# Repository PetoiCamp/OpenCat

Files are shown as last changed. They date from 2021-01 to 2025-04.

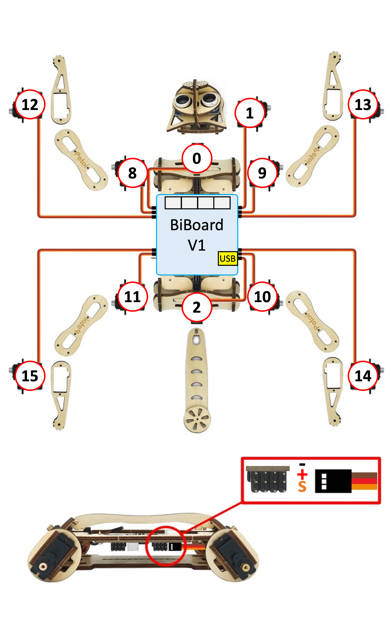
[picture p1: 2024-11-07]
pyUI/resources/NybbleQ1_Wire.jpeg

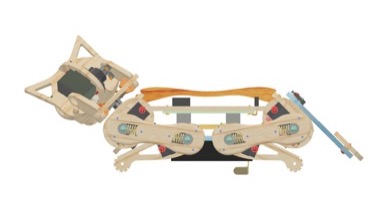
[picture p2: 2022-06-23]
pyUI/resources/Nybble_Rest.jpeg

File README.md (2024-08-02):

# OpenCat

OpenCat is the open-source Arduino and Raspberry Pi-based quadruped robotic pet framework developed by Petoi, the maker of futuristic programmable robotic pets.





Inspired by Boston Dynamics' Big Dog and Spot Mini, Dr. Rongzhong Li started the project in his dorm at Wake Forest University in 2016. After one year of R&D, he founded Petoi LLC and devoted all his resources to developing open source robots. 

The goal is to foster collaboration in quadruped(four-legged) robotic research, education, and engineering development of agile and affordable quadruped robot pets, bring STEM concepts to the mass, and inspire newcomers (including many kids and adults) to join the robotic AI revolution to create more applications.



The project is [a complex quadruped robot system](https://www.petoi.com/pages/petoi-programmable-quadruped-robot-system) for anyone exploring quadruped robotics. We want to share our design and work with the community and bring down the hardware and software costs with mass production. OpenCat has been deployed on all Petoi's bionic palm-sized, realistic lifelike [cute robot cat Nybble](https://www.petoi.com/collections/robots/products/petoi-nybble-robot-cat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) and
[high-performance robot dog Bittle](https://www.petoi.com/collections/robots/products/petoi-bittle-robot-dog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). We now have established a production line and can ship these [affordable robotic kits and accessories](https://www.petoi.com/store?utm_source=github&utm_medium=code&utm_campaign=store) worldwide.

This project provides a base open source platform to create amazing programmable gaits, locomotion, and deployment of inverse kinematics quadruped robots and bring simulations to the real world via block-based coding/C/C++/Python programming languages.  

Our users have deployed many robotics/AI/IoT applications:
- [robot dog with autonomous movement & object detection](https://www.petoi.com/blogs/blog/reid-graves-robotics-ai-applications-with-bittle-robot-dog-raspberry-pi)
- [Raspberry Pi robotics projects](https://www.petoi.com/blogs/blog/raspberry-pi-robotics-projects-with-petoi-open-source-quadruped-robots)
- [NVIDIA Issac simulations and reinforcement learning on our robots](https://www.youtube.com/playlist?list=PLHMFXft_rV6MWNGyofDzRhpatxZuUZMdg)
- [developed visual and lidar-based SLAM with ROS using Bittle and Raspberry Pi](https://www.youtube.com/watch?v=uXpQUIF_Jyk&list=PLHMFXft_rV6MWNGyofDzRhpatxZuUZMdg&index=6)
- [imitation learning using Tiny Machine Learning Models with Petoi Bittle and Raspberry Pi](https://www.learnwitharobot.com/p/imitation-learning-with-petoi-bittle)
- [IoT automation of a robot fleet with AWS to improve worker safety](https://www.petoi.com/blogs/blog/aws-iot-robot-fleet-demo-with-petoi-bittle)
- [3D-Printed Accessories](https://www.petoi.com/blogs/blog/petoi-bittle-bittle-x-robots-3d-printed-robot-accessories)
- build their own [DIY 3D-print robot pets](https://www.petoi.com/pages/3d-printed-robot-dog-robot-cat) powered by OpenCat





We've successfully crowdfunded these two mini robot kits and shipped thousands of units worldwide. 

With our [customized Arduino-Uno board](https://www.petoi.com/products/nyboard-customized-arduino-board) and [high-performance servos](https://www.petoi.com/products/quadruped-robot-dog-bittle-servo-set) coordinating all instinctive and sophisticated movements(walking, running, jumping, backflipping), one can clip on [various sensors](https://www.petoi.com/products/petoi-sensor-pack) and [camera](https://www.petoi.com/products/intelligent-camera-module) to bring in perception and inject artificial intelligence capabilities by mounting a Raspberry Pi or other AI chips(such as Nvidia Jetson Nano) through wired/wireless connections. 
 
Please see [Petoi FAQs](https://www.petoi.com/pages/faq?utm_source=github&utm_medium=code&utm_campaign=faq) for more info.

Also, Check out [all of the OpenCat and Petoi robot user showcases](https://www.petoi.camp/forum/showcase).



## Setup  Process:

OpenCat software works on both Nybble and Bittle, controlled by NyBoard based on ATmega328P. More detailed documentation can be found at the [Petoi Doc Center](https://docs.petoi.com).

To configure the board:

1. Download the repo and unfold. Remove the **-main** (or any branch name) suffix of the folder.

2. Open the file OpenCat.ino, select your robot and board version.
```cpp
#define BITTLE    //Petoi 9 DOF robot dog: 1x on head + 8x on leg
//#define NYBBLE  //Petoi 11 DOF robot cat: 2x on head + 1x on tail + 8x on leg

//#define NyBoard_V0_1
//#define NyBoard_V0_2
#define NyBoard_V1_0
//#define NyBoard_V1_1
```

3. Comment out ```#define MAIN_SKETCH``` so that it will turn the code to the board configuration mode. Upload and follow the serial prompts to proceed.
```cpp
// #define MAIN_SKETCH
```

4. If you activate ```#define AUTO_INIT```, the program will automatically set up without prompts. It will not reset joint offsets but calibrate the IMU. It's just a convenient option for our production line.

5. Plug the USB uploader to the NyBoard and install the driver if no USB port is found under Arduino -> Tools -> Port.

6. Press the upload button (->) at the top-left corner in Arduino IDE.

7. Open the serial monitor of Arduino IDE. You can find the button either under Tools, or at the top-right corner of the IDE.

Set the serial monitor as **no line ending** and **115200** baud rate.
The serial prompts:
```
Reset joint offsets? (Y/n)
Y
```

Input ‘Y’ and hit enter, if you want to reset all the joint offsets to 0.

The program will do the reset, then update the constants and instinctive skills in the static memory.

8. IMU (Inertial Measurement Unit) calibration.

The serial prompts:
```
Calibrate the IMU? (Y/n):
Y
```
Input ‘Y’ and hit enter, if you have never calibrated the IMU or want to redo calibration.

Put the robot flat on the table and don't touch it. The robot will long beep six times to give you enough time. Then it will read hundreds of sensor data and save the offsets. It will beep when the calibration finishes.

When the serial monitor prints "Ready!", you can close the serial monitor to do the next step.

9. Uncomment ```#define MAIN_SKETCH``` to make it active. This time the code becomes the normal program for the major functionalities. Upload the code.
```cpp
#define MAIN_SKETCH
```
When the serial monitor prints "Ready!", the robot is ready to take your next instructions.

10. If you have never calibrated the joints’ offsets or reset the offsets in Step2, you need to calibrate them. If you boot up the robot with one side up, it will enter the calibration state automatically for you to install the legs. Otherwise, it will enter the normal rest state

11. You can use the serial monitor to calibrate it directly. Or you may plug in the Bluetooth dongle, and use the Petoi app (on Android/iOS) for a more user-friendly interface. The mobile app is available on:

* IOS: [App Store](https://apps.apple.com/us/app/petoi/id1581548095)
* Android: [Google Play](https://play.google.com/store/apps/details?id=com.petoi.petoiapp)

You can refer to the calibration section in the user manual (https://bittle.petoi.com/6-calibration) and Guide for the Petoi App(https://docs.petoi.com/app-guide).

12. you can use the infrared remote or other applications (such as the Petoi App, Python, serial monitor ... etc.) to play with the robot (https://bittle.petoi.com/7-play-with-bittle).

For updates:
* star this repository to receive timely notifications on changes.
* visit www.petoi.com and [subscribe to our official newsletters](https://www.petoi.com/pages/subscribe-petoi-newsletter) for project announcements. We also host a forum at [petoi.camp](https://www.petoi.com/forum).
* follow us on [Twitter](https://twitter.com/petoicamp), [Instagram](https://www.instagram.com/petoicamp/), [Facebook](https://www.facebook.com/PetoiCamp/), [Linkedin](https://www.linkedin.com/company/33449768/admin/dashboard/), and [YouTube channel](https://www.youtube.com/c/rongzhongli) for fun videos and community activities.



## Resources:
* [Advanced tutorials made by users](https://www.youtube.com/playlist?list=PLHMFXft_rV6MWNGyofDzRhpatxZuUZMdg)
* [Review, open-box, and demos by users](https://www.youtube.com/playlist?list=PLHMFXft_rV6PSS3Qu5yQ-0iPW-ohu1sM3)
* [OpenCat robot showcase by users](https://www.petoi.com/pages/petoi-open-source-extensions-user-demos-and-hacks)
* [OpenCat robot gallery](https://www.petoi.com/pages/robot-pet-gallery)

OpenCat robots have been used in robotics education for K12 schools and colleges to teach students about STEM, coding, and robotics:
- [robotics education showcases](https://www.petoi.com/blogs/blog/tagged/showcase+education)
- [STEM & Robotics Curriculum & Resources for Teaching Coding & Robotics](https://www.petoi.com/pages/resources-curriculum-stem-coding-robot)
- [Robotics competitions](https://www.petoi.com/blogs/blog/robot-competitions-with-petoi)
- [Petoi robotics contest](https://www.petoi.com/blogs/blog/petoi-spring-2024-robotics-contest-winners)

The [old repository for OpenCat](https://github.com/PetoiCamp/OpenCat-Old) is too redundant with large image logs and is obsolete with no further updates.

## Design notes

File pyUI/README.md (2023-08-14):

# Petoi Desktop App 
## The source codes are written with Tinker in Python3 

The major function modules are the [Firmware Uploader](https://docs.petoi.com/desktop-app/firmware-uploader), [Joint Calibrator](https://docs.petoi.com/desktop-app/calibrator), and [Skill Composer](https://docs.petoi.com/desktop-app/skill-composer). 

**UI.py** is the general entry for all the modules:

- UI.py

-> FirmwareUploader.py

-> Calibrator.py

-> SkillComposer.py

gui

**translate.py** provides multi-language support for the UI. You may help to translate the UI into your language. 

Before running the app, you need to use the included USB adapter or the Bluetooth dongle to connect to a Petoi robot. 

## Pre-compiled binaries

You can download the [pre-compiled binaries](https://github.com/PetoiCamp/OpenCat/releases).

Windows users:
Double-click the exe file to run the app. Keep all the files in the Win folder when moving the app. 

Mac users:
Double-click the dmg file and drag the app to the Application folder. Go to the Application folder and right-click the Petoi icon. Hold the **shift** key, then click **Open**.

## Run the app from the Terminal 
In the case of compatibility issues, or if you want to modify the source and test, you can also run the code from the Terminal. 

The Terminal is a built-in interface on Mac or Linux machines. The equivalent environment on Windows machines is called the Command-Line Tool (CMD). 
It's recommended that you install [Anaconda](https://www.anaconda.com/) to manage your Python environment. It can also provide the Powershell as a Terminal for older Windows machines. 

Depending on your existing Python configuration, you may need to upgrade to Python3 and install the following libraries:

- pyserial
- pillow

You can install them by entering ```pip3 install pyserial pillow``` in the Terminal or use the package manager in Anaconda. 

To run the code:
1. In the Terminal, use the ```cd``` command to navigate to the ```OpenCat/pyUI/``` folder. You can use the Tab key to auto-complete the path name. 
2. After entering the pyUI/ folder, enter ```ls``` and ensure you can see the UI.py and other python source codes listed. 
3. Enter ```python3 UI.py```.

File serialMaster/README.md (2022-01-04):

## serialMaster User Guide

**Preparation**

1.  Install python (version≥ 3.6, such as Anaconda3-5.2.0-Windows-x86_64.exe)
    
2.  Install pyserial library (version 3.5)
    
**Run script**

The script program will automatically identify the serial port number at the very beginning of the run, and complete the connection.

Generally, when using a USB adapter to connect to Nybble (or Bittle), there is only one serial port number:

USB serial port number

When using the Bluetooth module, there are two serial port numbers:

Bluetooth serial port number

Open Terminal (such as Anaconda Prompt), enter the path where the script is located (***\serialMaster), you can use the following command to run the script:

**Method 1**: Run the **ardSerial.py**

***\serialMaster>python3 ardSerial.py kbalance

Parameters: **kbalance** is a serial port command representing Nybble (or Bittle) skills.

Of course, you can also run this script without any parameters:

***\serialMaster>python3 ardSerial.py

When the system recognizes that there are multiple serial port numbers, the script will print out the following prompt message at the very beginning of the run:

**If there is no response after you input the serial command in the terminal, you should close the terminal first, then change the value of "bluetoothPortIndex" in the ardSerial.py (line:128)to connect to another blue tooth serial port, then reopen the terminal and rerun the script.**

When the script formally starts running, the following prompt information is printed out:
**You can type 'quit' or 'q' to exit.**

Next, you can enter serial port commands in Terminal to control Nybble (or Bittle) to do various interesting actions e.g.

kbalance           # Command to control Nybble(or Bittle) to stand normally

m 0 -30 0 30       # Command to control Nybble(or Bittle) head to swing left and right

**Method 2**: Run a custom script, e.g.  **example.py**

***\serialMaster>python3 example.py

The list **testSchedule** in example.py is used to test various serial port commands. Run the following script code to see the execution effect of each serial port command in the list:

for task in testSchedule:
	wrapper(task)

You can also refer to the content of the **stepUpSchedule** list (in***\serialMaster\demos\stepup.py), write a list of behaviors according to your actual needs, and realize your creativity.

**Note**: When running the scripts under the path **"***\serialMaster\demos"**, you must first use the **"cd demos"** command to enter the path where the scripts are located (\serialMaster\demos), and then use the **python3** command to run the script. e.g. 
***\serialMaster\demos>python3 stepup.py

Explanation of the serial port commands in the list**testSchedule**:

**['kbalance', 2]**
-   'kbalance' indicates the command to control Bittle to stand normally
-   2 indicates the postponed time after finishing the command, in seconds

**['m', [0, -20], 1.5]**
- m indicates the command to control the rotation of the joint servo
-   0 indicates the index number of joint servo
-   -20 indicates the rotation angle (this angle refers to the origin, rather than additive) the unit is degree
-   1.5 indicates the postponed time after finishing the command, in seconds. It can be a float number

**['m', ['m', '0', '45', '0', '-45', '0', '45', '0', '-45'], 2]**

Using this format, multiple joint servo rotation commands can be issued at one time, and these joint servo rotation commands are executed **SEQUENTIALLY**, not at the same time.
The meaning of this example is: the joint servo with index number 0 is first rotated to the 45 degree position, and then rotated to the -45 degree position, and so on. After these motion commands are completed, the next command will be executed after a 2-second delay.

**['M', ['M', '8', '-15', '9', '-20'], 2]**

Using this format, multiple joint servo rotation commands can be issued at one time, and these joint servo rotation commands are executed **AT THE SAME TIME.**
The meaning of this example is the joint servos with index numbers 8, 9 are rotated to the -15, -20 degree positions at the same time. After these motion commands are completed, the next command will be executed after a 2-second delay.

**['d', 2]**
-   d indicates the command to put the robot down and shut down the servos
-   2 indicates the postponed time after finishing the command, in seconds

**['c', 2]**
-   c indicates the command to enter calibration mode
-   2 indicates the postponed time after finishing the command, in seconds. After these motion commands are completed, the next command will be executed after a 2-second delay.

**['c', [0, -9], 2]**
-   c indicates the command to enter calibration mode
-   0 indicates the index number of joint servo
-   -9 indicates the rotation angle, the unit is degree
-   2 indicates the postponed time after finishing the command, in seconds

Using this format, you can enter the calibration mode to calibrate the angle of a certain joint servo.
**Note**: If you want the correction value in this command to take effect, you need to enter the "**s"**command after executing this command.
The meaning of this example: the joint servo with serial number 0 rotates -9 degrees. After these motion commands are completed, the next command will be executed after a 2-second delay.

**['i', [8, 50, 9, 50, 10, 50, 11, 50, 0, 0], 3]**
-   i indicates the command to rotate multiple joint servos at the same time
-   8, 9, 10, 11, 0 indicate the index numbers of joint servos
-   50, 50, 50, 50, 0 indicate the rotation angle (this angle refers to the origin, rather than additive ), the unit is degree
-   3 indicates the postponed time after finishing the command, in seconds
 
**['l', [20, 0, 0, 0, 0, 0, 0, 0, 45, 45, 45, 45, 36, 36, 36, 36], 5]**
-   l indicates the command to control all joint servos to rotate at the same time (currently the command supports 16 degrees of freedom, that is, 16 servos)
-   20,0,0,0,0,0,0,0,45,45,45,45,36,36,36,36 indicate the rotation angle of each joint servo corresponding to 0-15 (this angle refers to the origin, rather than additive), the unit is degree
-   5 indicates the postponed time after finishing the command, in seconds

**['b', [10, 255], 2]**
-   b indicates the command to control the buzzer to beep
-   10 indicates the music tone
-   255 indicates the lengths of duration, the value range is 0~255 
-   2 indicates the postponed time after completing the pronunciation, in seconds

**['b', ['b', '14', '90', '14', '90', '21', '90', '21', '90', ‘23', '90', '23', '90', '21', '180'], 5]**
-   b indicates the command to control the buzzer to beep
-   '14', '14', '21', '21', ‘23', '23', '21' indicate the music tones
-   '90', '90', '90', '90', '90', '90', '180' indicates the lengths of duration
-   5 indicates the postponed time after the music melody is played, in seconds

Using this format, multiple tone pronunciation commands can be issued at one time, and a simple melody can be played.
The meaning of this example is: play a simple melody, and delay 5 seconds after the music melody is played.

For the description of other serial port commands, please refer to Chapter 7 of the Petoi Bittle User Manuals:
[7 🕹 Play with Bittle](https://bittle.petoi.com/7-play-with-bittle)

Please help Nybble and Bittle find their sparks. Wish you have fun!

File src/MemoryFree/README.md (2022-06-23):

This is the excellent MemoryFree library from http://www.arduino.cc/playground/Code/AvailableMemory.

I am hosting it here so there is a quick and easy way to pull it down.

(20 Mar 2015) Repository updated with code from http://playground.arduino.cc/code/AvailableMemory

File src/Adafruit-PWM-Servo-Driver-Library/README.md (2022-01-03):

# Adafruit PCA9685 PWM Servo Driver Library 

This is a library for our Adafruit 16-channel PWM & Servo driver, shield or FeatherWing



Pick one up today in the adafruit shop!
  * https://www.adafruit.com/products/815
  * https://www.adafruit.com/product/1411
  * https://www.adafruit.com/product/2928

These drivers use I2C to communicate, 2 pins are required to interface.

Adafruit invests time and resources providing this open source code, please support Adafruit and open-source hardware by purchasing products from Adafruit!

Written by Limor Fried/Ladyada  for Adafruit Industries. BSD license, check license.txt for more information. 

All text above must be included in any redistribution

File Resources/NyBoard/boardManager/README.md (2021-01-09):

# Arduino IDE Board Manager

Adds the NyBoard board definition through the *Arduino 1.6.4 (and later)* board manager rather then editing `boards.txt` directly as described at https://github.com/PetoiCamp/OpenCat/wiki/Software-setup.

## Usage

1. Open the Arduino IDE application

2. Open the `Preferences...` panel

3. In the `Additional Boards Manager URLs` field, add `https://raw.githubusercontent.com/PetoiCamp/OpenCat/master/Resources/NyBoard/boardManager/package_petoi_nyboard_index.json`. If there are already URLs listed in this field, separate them with commas or click on the icon next to the field to open up an editor and add this URL to a new line.

4. Click on the `OK` button to close the `Preferences...` panel (you may need to do this for the `Additional Boards Manager URLs` editor first, if you opened it up in the previous step)

5. Open the `Boards Manager...` window with the `Tools` -> `Board: XXXX` -> `Boards Manager...` menu item.

6. In the `Filter your search...` field, type `NyBoard`

7. Select the entry and click on `Install`

8. Click on the `Close` button

9. Select `ATmega328P (5V, 20 MHz) NyBoard` from the `Tools` -> `Board: XXXX` menu and enjoy!

## Updating the Board Definition

This section should not be necessary for most users and is included only for reference. As this is my first foray into using the Boards Manager, these steps may change slightly as necessary and I will try to keep this updated for reference.

1. Any additions to the `NyBoard-0.1` directory or changes to `NyBoard-0.1/boards.txt` require the following additional steps (update version numbers as appropriate):

  A. The archive file `NyBoard-0.1.x.tar.bz2` needs to be rebuilt

    i. Mac or Linux, use: `tar -cjf NyBoard-0.1.x.tar.bz2 NyBoard-0.1`

    ii. *TBD* need Windows equivalent

  B. Update `pacakge_petoi_nyboard_index.json` as follows:

    i. Update the `"version"` field to match the new version number (e.g. "0.1.x")

    ii. Update the `"url"` and `"archiveFileName"` fields to match the new archive name.

    iii. Update the `"size"` field to match the new archive file size

    iv. Update the `"checksum"` field to match the new archive file

      a. Mac or Linux use: `openssl dgst -sha256 NyBoard-0.1.x.tar.bz2` to get this value

      b. *TBD* need Windows equivalent

  C. Alternatively, if you wish to keep multiple versions of the board definition around, you can copy the entire entry in `"platforms"` (lines 12 - 31), add a comma after the closing brace of the last entry in `"platforms"`, paste the copy to the next line (before the closing bracket) and make the changes in **B** to the new entry.

2. Changes to the other informational fields of `pacakge_petoi_nyboard_index.json` should not require rebuilding the archive or modifying the file size or checksum values.

## Reference

* https://github.com/PetoiCamp/OpenCat/wiki/Software-setup
* https://github.com/arduino/Arduino/wiki/Arduino-IDE-1.6.x-package_index.json-format-specification

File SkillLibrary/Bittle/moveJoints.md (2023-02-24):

# moveJoints
Note: A test case to send the movement to the smartphone app.

Model: Bittle

Creator: Rz Li

Country: China

Date: Feb 10, 2023

# Token
I

# Data
{
8, -15, 9, -20};

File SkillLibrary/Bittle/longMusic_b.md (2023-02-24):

# longMusic_b
Note: A test case to send the long music to the smartphone app.

Model: Bittle

Creator: Rz Li

Country: China

Date: Feb 10, 2023

# Token
b

# Data
{ 
14, 8, 14, 8, 21, 8, 21, 8, 23, 8, 23, 8, 21, 4, 19, 8, 19, 8, 18, 8, 18, 8, 16, 8, 16, 8, 14, 4, 21, 8, 21, 8, 19, 8, 19, 8, 18, 8, 18, 8, 16, 4, 21, 8, 21, 8, 19, 8, 19, 8, 18, 8, 18, 8, 16, 4,  14, 8, 14, 8, 21, 8, 21, 8, 23, 8, 23, 8, 21, 4, 19, 8, 19, 8, 18, 8, 18, 8, 16, 8, 16, 8, 14, 4};

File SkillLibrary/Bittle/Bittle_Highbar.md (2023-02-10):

# Highbar
Note: Make Bittle roll on a high bar 111 times. Change the 111 to -1 to make it infinite. You need to install the [hooks](https://github.com/PetoiCamp/NonCodeFiles/tree/master/stl/BittleHighbarHooks) on Bittle's front hands. 

Model: Bittle

Creator: David Lin

Country: China

Date: July 18, 2022

# [Demo](https://youtu.be/kam61UxwSVc)

# Token
K

# Data

{
  -3,   0,   0,   2,
   1,   2, 111,
   0,   0,   0,   0,   0,   0,   0,   0, -61, -61,  30,  30,  45,  45,  75,  75,  32,   0,   0, -90,
   0,   0,   0,   0,   0,   0,   0,   0,  28,  28,  21,  21,  25,  25,  44,  44,  48,   0,   0,  10,
   0,   0,   0,   0,   0,   0,   0,   0, -61, -61,  30,  30,  45,  45,  75,  75,   0,   0,  -1, -90,
};

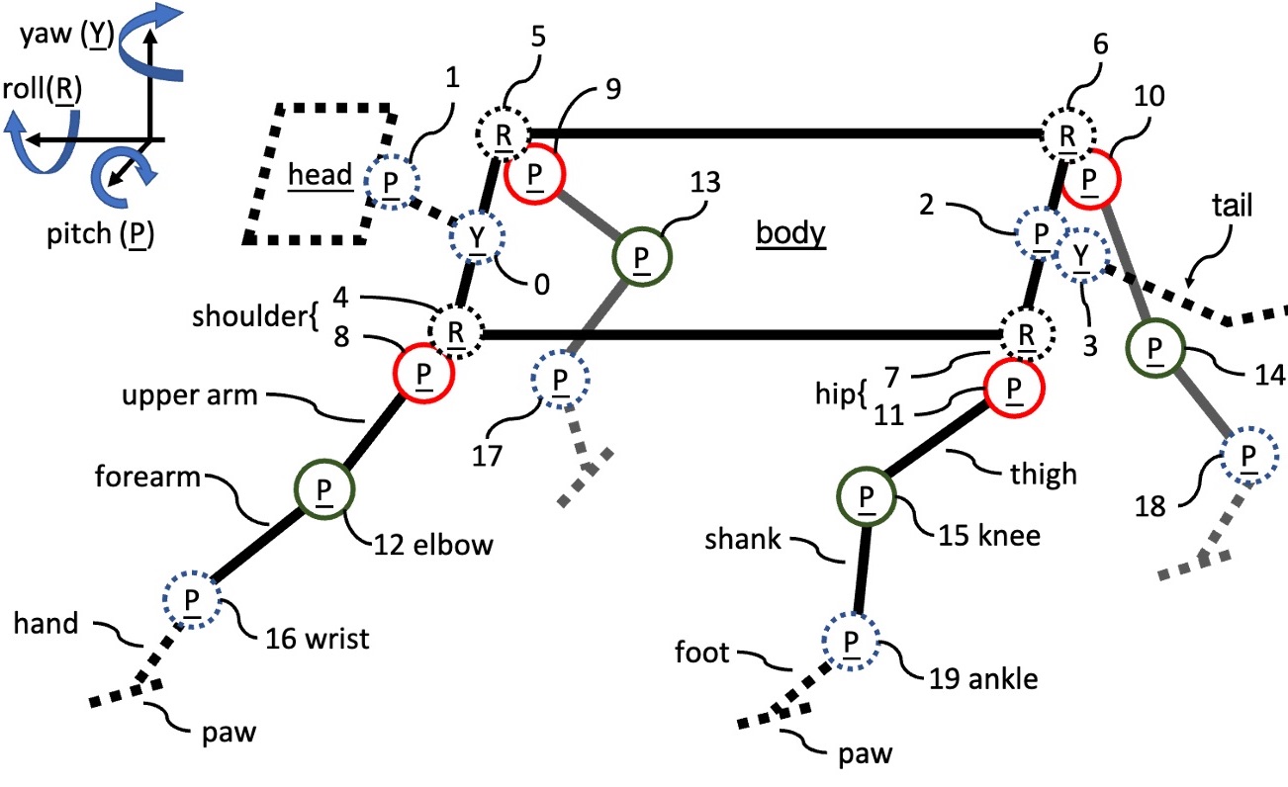
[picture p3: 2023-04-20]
pyUI/resources/DoF16_Stand.jpeg

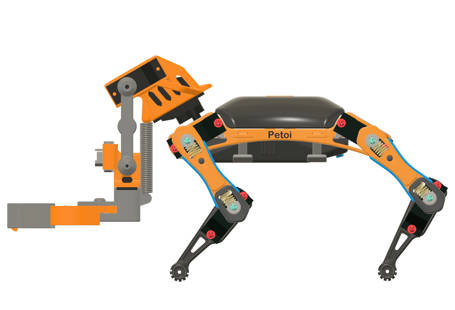
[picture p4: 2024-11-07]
pyUI/resources/BittleX+Arm_Stand.jpeg

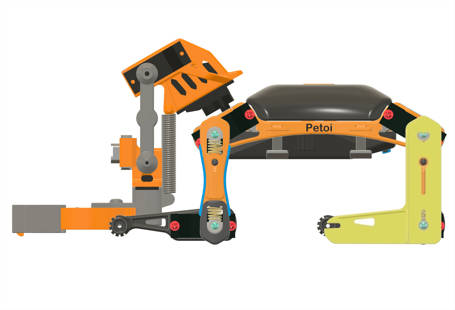
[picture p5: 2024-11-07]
pyUI/resources/BittleX+Arm_Ruler.jpeg

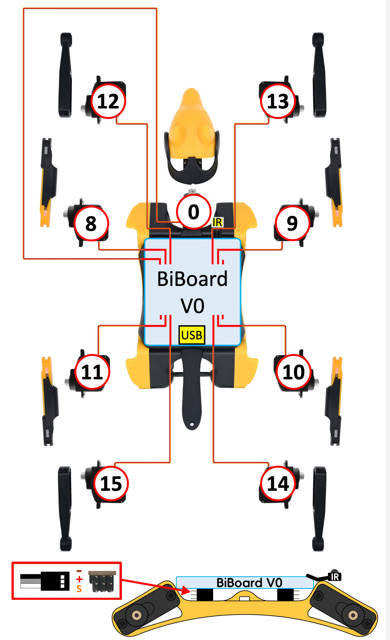
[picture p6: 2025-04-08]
pyUI/resources/BittleX0_Wire.jpeg

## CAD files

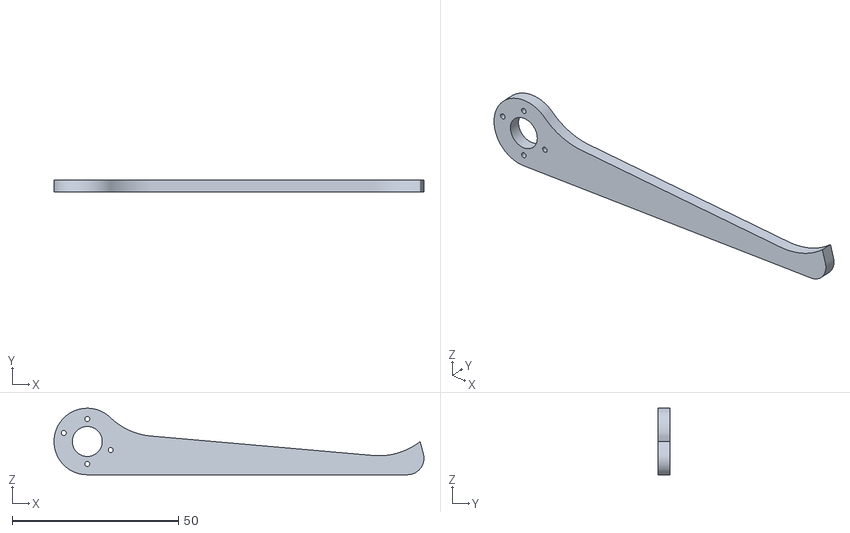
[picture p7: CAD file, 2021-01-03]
ModuleTests/testServo/servoTorqueArm.stl
111.2 x 3.50 x 20.0

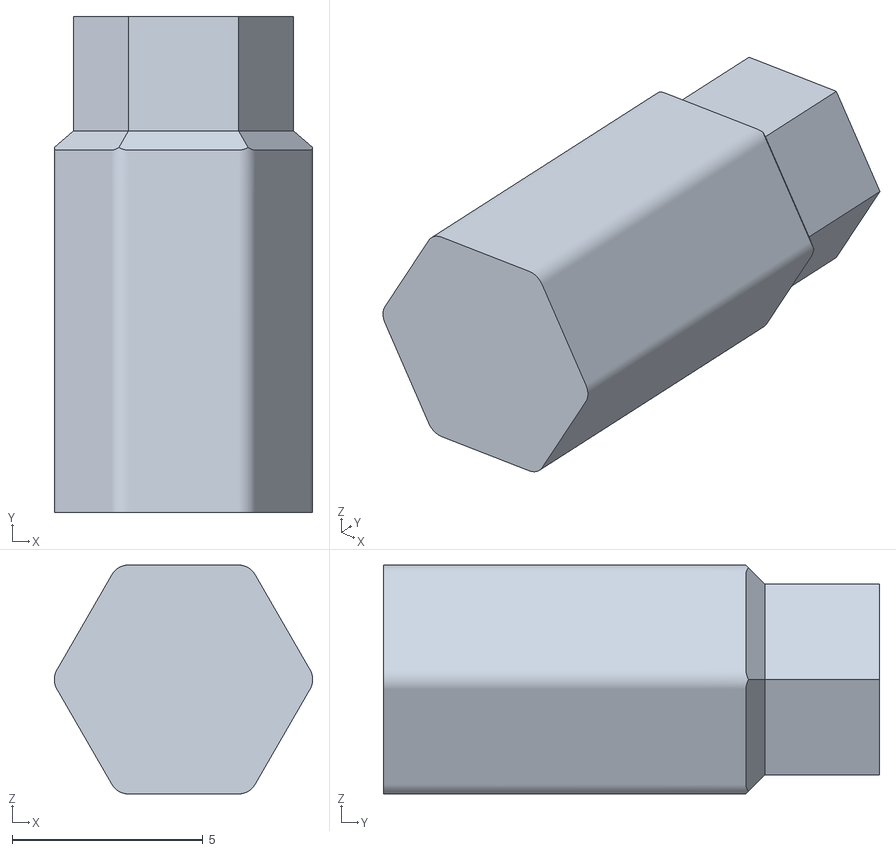
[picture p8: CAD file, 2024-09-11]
pyUI/resources/tool.stl
6.77 x 13.0 x 6.00

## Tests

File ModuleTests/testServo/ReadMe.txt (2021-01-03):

The video for the tests can be found at https://youtu.be/vCvjGVeO57g

Datasheet is at https://docs.google.com/spreadsheets/d/1R2a6Q3H9Heo5MBXjv3MdyxipxWbeRYw3lmymrDakhaY/edit?usp=sharing

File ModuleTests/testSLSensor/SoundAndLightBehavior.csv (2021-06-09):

LIGHT | READING | THRESHOLD
brighter | lower
darker | higher | 850
LIGHT |  | SOUND
_LEVEL | _CHANGE | _LEVEL | _BEHAVIOR
dark |  | low | rest
 |  | high | sit
high |  | low | sit
 |  | high | stand
 | fast light
 | fast dim
bright |  |  | proportional

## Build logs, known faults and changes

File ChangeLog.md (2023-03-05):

# Change Log

## Mar6, 2023
* Recover the skillName stored in **newCmd** array because the newCmd's memory is altered when formatting new skill data. 
* Fix the segfault caused by different string terminators: '\0', '\n', or '\~'.
* Fix the casting between int, char, and int8_t in the template function arrayNCPY().
* When turning a joint instruction into a new posture, allow large joint angles to be stored into an int8_t array. 
* Fix the positive feedback when gyro data is combined into targetAngles.
* SkillComposer: Disable the Gyro and Random buttons.
* ardSerial: Simplify the slicing algorithm when sending long commands.
* Differentiate the serial timeout for long commands over Bluetooth.
* Simplify some skills to save memory. 
* Safer auto-connection algorithm when trying to connect to a camera that's not connected to any alternative addresses. 
* Mobile app: Find the optimal delay between the mobile app's package slices to avoid overflow or timeout on the mainboard. 
* Add a token 'S' to toggle on/off the boot-up melody. 
* Add a macro to inverse the servo's rotation directions.
* Allow the robot to detect the falling-over event and recover even in turbo mode. 
* Desktop App: Add traditional Chinese and German translations. 

## Mar 1, 2023
* Combine the **newCmd** array used for receiving different kinds(ASCII/Binary, long/short) of serial commands. 
* Simplify the token cases into upper/lower letters for Binary/ASCII encodings.
* Shift the skill angle data to the end of the **newCmd** array. It allows new incoming messages to be stored at the beginning of the **newCmd** array while keeping the skill angles unchanged so that the previous skill can resume after finishing the current non-skill command. 
* It now supports much longer commands and skills, such as a behavior with **23** frames (23 * 20 + 7 = 467 bytes), a gait with (467-4)/8 = **57** frames or a long melody with 467/2 = **233** notes. On BiBoard, it supports a behavior with **125** frames (125 * 20 + 7 = 2507 bytes), a gait with (2507-4)/8 = **312** frames or a long melody with 2507/2 = **1253** notes.
* Overflow protection when the incoming message is longer than the size of **newCmd** to avoid a crash. 
* Redesign the voice commands table and their encodings. 
* Add an alias skill "up" for "balance" to save memory and convenience. 
* Move the keys of the customized voice commands to PROGMEM.
* Add new skills:

| New Skill Name | Serial Code |
|---|:---|
|hug 	|khg |
|handstand  |khdsd  |
|hands up |khu 	  |
|handshake	|khsk  	|
|sniff		  |ksnf	  |
|dig	 	|kdg	  |
|scratch |kscrh  |
|be table 	|ktbl	  |
|boxing	  	|kbx	  |
|kick		 |kkc	  |
|come here	|kcmh	  |
|high five	|kfiv	  |
|jump		 |kjmp	  |

* With so many new skills saved to the I2C EEPROM, fix the overflow (wrapped overwriting) when a long 'K' skill data is written to the nearly full memory.
* 'T' token is used to extract the last transferred skill data. Fixed the segfault when a newly configured board has never received a 'K' command but is required to read from an unknown memory. 

## Feb 25, 2023
* Unbind the free joints' motion during walking and keep balancing reaction after the i,I,m,M commands. The free joints are unrelated to walking and balancing. By default, they move by trigonometric functions synced with the legs' pace. If a command requires specific joint movement, it will be unbound and taken over by the higher-level controller. Using the token 'i' or 'I' without more argument will re-bind them to the legs' motion.

When sending joint instructions, the rules are:

| |All are free joints (head, tail, etc.) |Contain joints related to walking|
|:---:|---|---|
|Gait			 |move in perform() => gait  	  |move in tranform() => convert to a new posture	|
|Posture |move in perform() => posture  |move in tranform() => convert to a new posture	|
|Non-skill |move in transform() => lastToken|move in tranform() => convert to a new posture => lastToken|

* Allow explicitly assigning directions of skills. Only the neutral and the leftward skills are stored in the skill table with the suffix -F (only for gaits), -L, or no capitalized letter in the key. Previously all skills are called with random directions, except the gaits. 

Let Name be the skill's name. The new rules are:

| | Match? |Mirror it? |
|---|:---:|:---:|
|gaitF  |All characters |N |
|nameL  |All characters |N |
|nameR  |the first n-1 chars  |Mirror nameL |
|name		|All characters |Random	 |
|nameX  |All characters 	 |Random |

* Debug the creation, pop, and deletion of TaskQueue for safer and more efficient memory management. Optimize the corresponding examples for light, touch, pir, gesture, camera, and voice sensors.

## Feb 10, 2023
* Allow controlling head group while walking.
* Solve serial overflow.
* Add random skill command: kx. It can call a random skill in the preset skill list. 
* Add macros to disable some unused tokens to save space.

## Feb 7, 2023
* Improve the serial read logics. 
* Print software version on boot up.
* Add demos for pir, touch, light modules.
* Allow sending long (450 bytes or 225 notes) melody over the serial port.

## Feb 1, 2023
* Add task queue within the Arduino code. A sequence of tasks can be performed without the need of another master computer. 
* Add demo code for 10 customized voice commands. 

## Jan 19, 2023
* Allow manually select the serial port when the automatic algorithm fails.

## Jan 12, 2023
* Add demo code for the voice command module. 
* SkillComposer: Allow importing multiple skills from InstinctX.h.

## Jan 5, 2023
* Avoid the servos' shaking when booting up.
* Add demo code for the gesture module.

## Dec 29, 2022
* SkillComposer: Avoid freezing when dragging the joint sliders.

## Dec 26, 2022
* Allow a unplug and replug algorithm to tell the intended serial port.
* SkillCompser: Read the robot's name when starting up.

## Dec 13, 2022
* Improve the self-calibration algorithm of PCA9685

## Dec 7, 2022
* SkillComposer: Show warning forlower Python versions.

## Nov 28, 2022
* FirmwareUploader: Support BiBoard.

## Nov 10, 2022
* Create test8266Master.ino that can control the robot's motion in sequence.

## Oct 26, 2022
* Move the detailed initializing functions in **OpenCat.ino**'s setup() to OpenCat.h. 
* Add a simple example to elaborate the integration of customized sensors. You need to enable "#define OTHER_MODULES" to see its effects. 

## Aug 31, 2022
* Add a watchdog to reset the board if the initialization for MPU or skills fails.
* At the last stage of the first configuration process (with #define MAIN_SKETCH commented out), provide an optional step to calibrate the PCA9685's PWM frequency. The calibration value is saved in the EEPROM table to be loaded by the main sketch. 
* Change the unit of the duration for music notes ('b' and 'B' token) from duration (miliseconds) to half notes (use 2, 4, 8 to represent 1/2, 1/4, 1/8).
* For Bittle: Add front flip, roll left, roll right, and tune back flip. It's better to remove its head to perform those tricks. 
* Shrink the size of codes for getting and saving MPU offsets.
* Won't repeat the last behavior after roll recover.
* ESP8266WiFiController: won't refresh the page after sending command to save time
* ESP8266WiFiController: Simplify the cases on the main command page with a dictionary. 
* Add some new moduleTest codes

## May 8, 2022
* pyUI/ui.py: Add names to trigger axis
* pyUI/ui.py: Optimize the layout for Windows machines
* pyUI/ui.py: Add add hover tips to some buttons

## May 4, 2022
* pyUI/ui.py: Import and export files

## May 2, 2022
* pyUI/ui.py: Improve performance with large angles
* pyUI/ui.py: Show connected ports
* pyUI/ui.py: Improve logic and workflow for connecting multiple robots
* pyUI/ui.py: Support connect to one or all robots dynamically
* pyUI/ui.py: Improve global orientation and translation sliders
* pyUI/ui.py: Change dial buttons from regular buttons to press-down buttons

## Apr 30, 2022
* pyUI/ui.py: Mirror single frame during editing
* pyUI/ui.py: Fix bug in the loop structure when exporting 

## Apr 29, 2022
* pyUI/ui.py: Add binders (both positive and negative) for joint sliders to control several joints together.
* pyUI/ui.py: Can control multiple robots at once. 
* ardSerial: Get return value from threads.

## Apr 24, 2022
* pyUI/ui.py: Support loading and sending large angles
* pyUI/ui.py: Optimize panel sizes

## Apr 22, 2022
* pyUI/ui.py: Support selecting different robot models. Update the center image for the model. 
* pyUI/ui.py: Support different lanuguages.
* pyUI/ui.py: Support importing and exporting a multi-frame skill as a behavior or gait. A single frame will always be exported as a posture.
* pyUI/ui.py: Update the skill frame's state for delete operations.
* pyUI/ui.py: Check the format of skill data that's manually entered. Pop up a warning window.  

## Apr 20, 2022
* pyUI/ui.py: Support trigger axis and angles for behaviors
* pyUI/ui.py: Allow stop when playing frames
* Add a button to connect and disconnect the robot in the "State Dials" block
* Change the texts of the state dials to indicate their states

## Apr 19, 2022
* pyUI/ui.py: Support importing existing skill array and editing them frame by frame. Speed and delay are included. The trigger axis of behaviors has not been implemented.
* pyUI/ui.py: Export the skill to the robot and print the skill data array in the terminal. 

## Apr 6, 2022
* Add ui.py in pyUI to allow changing the robot's postures and body tilts with sliders. 
* Improve the structure of ardSerial.py to allow continuous inputs when it's used as a commandline tool. 
* Fix a bug when a static posture is called after a gait by resetting the frame to 0.

## Mar 29, 2022
* Use dataBuffer to hold the incoming serial commands to allow a longer melody and other instructions. newCmd will only be used to hold skill names that are shorter. 
* Save the serial skill data from the dataBuffer to I2C EEPROM so that it can be recalled. 

## Mar 20, 2022
* A schedulerToSkill function in serialMaster to summerize the motion commands and generate a new skill array that can be directly used in the instinct.h.
* Design a convenient macro switch for regular walker, ultrasonic, and voice modes. 
```cpp
//you can activate the following modes (they will diable the gyro to save programming space)
//allowed combinations: RANDOM_MIND, ULTRASONIC, RANDOM_MIND + ULTRASONIC, VOICE
//#define RANDOM_MIND     //let the robot do random stuffs. use token 'z' to activate/deactivate
//#define ULTRASONIC      //for Nybble's ultrasonic sensor
//#define VOICE           //for LD3320 module
```

## Mar 17, 2022
### OpenCat2.0 is pushed to the branch 2.0 for beta testers.
### New Features:
* **Complete redesign of the code structure to make it easier to understand and insert 3rd party codes.**
* **Combine WriteInstinct.ino and OpenCat.ino into a single OpenCat.ino.** Use the ```#define MAIN_SKETCH``` macro to switch between the modes. 
* Fixed many bugs in the original workflow. For example, the robot no longer skips commands randomly.
* Improved the smoothness of motion and the speed of balance adaption. 
* A better documented serialMaster Python module and provide a command scheduler in example.py. 
* **Designd a new token "K"** to send a whole skill array from the Python serial master through serial in realtime then run it locally on the robot.
* Optimized the token definitions. Print the token after finishing one task as a confirmation to the master program. 
* Used a new MPU6050 function to avoid using the interrupt pin. **Accelerate the IMU calibration process.** 
* Enter the joint calibration state by booting up the robot with one side up. 
* Write a formalized servo class inherited from the AdafruitPWM servo library. Make it easier to change parameters of 3rd party servos.
* **Use the built-in tone function to generate clean beeps and melody.**
* Add random actions for the robot to make it more life-like. Use token ‘z’ to turn on/off the feature. 
* Add angle limits to avoid most cases of of self-collision.
* Put the skill-related functions into the Skill Class. Combine reused code blocks into single functions.
* Make more use of the EEPROM and PRGMEM memory to save resources for flash and SRAM.
* Mirror rightward gaits from the leftward gaits, to save static memory. 
* Allow both “newline” and “no line ending” for the serial monitor.
* Add support for LD3320 voice recognition module (the current code works for Chinese).

## Jan 30, 2022
* Fix type conversion warnings of skill data.
* Add demo for testBuzzer.ino using Arduino's built-in tone function. However, it cannot be used for the main program because ATmega328P has only two timers, used up by the IR and IMU. 

## Jan 11, 2022
* Create a mirror function to allow the robot pick random directions of behaviors. It makes the robot more unpredictable and helps it get rid of an infinite loop, such as failed fall-recovering against a wall.  

## Jan 3, 2022
* Put the dependent libraries within the OpenCat folder so that no more downloading is required to configure OpenCat's environment in Arduino. 

It's nasty to include the **src/** libraries here rather than Arduino's desinated library folder, especially when we have to duplicate the **src/** in two layers within the same project folder.  

We do this only to help those users who are new to Arduino and complained about the difficulties of configuring the Arduino environment. You may find more informative comments within those library files. 

## Dec 29, 2021
* Organinzed serialMaster/ and its demo codes
* fixed the divide by zero bug in calibratedPWM()

## Dec 11, 2021
* Fix bug of "wrong key!" messages after g, p

## Dec 3, 2021
* Modified the "hi" behavior of Nybble so its tail will not push Nybble over;
* Replaced the "look up" behavior with "stand". Make sure you hold Nybble when first trying it. 

## Nov 28, 2021
* Add the march gait that only works well with gyro off; 
* Fix many typos with the help of Grammarly.

## Sep 29, 2021
* Print the robot's state (paused and gyro) when "g" and "p" is entered:

| State  | True  | False |
|:---|:---|:---|
| Pause | P (paused) | p (unpaused) |
| Gyro | G (on) | g (off) |

## Sep 26, 2021
* Move the codes for EEPROM to function configureEEPROM() in OpenCat.h;

## Sep 18, 2021
* Copied the required files of IRremote library to OpenCat/src/ to help new Arduino users config the environment. 
* Cancel "pause" of motion if other commands are received. 

## Sep 16, 2021
* Move the EEPROM related functions from WriteInstinct.ino to OpenCat.h.
* Added a "stand" behavior for Nybble so that it can stand up with its hind legs and tail. 

## Sep 9, 2021
* Print the list of calibration offsets before the joints' movements to help the App read the values.

## Aug 31, 2021
* Moved the device's model info (Nybble/Bittle) to the top of booting printouts.
* Added a shorter encoding for the IR remote to save flash by about 178 Bytes.

## Aug 25, 2021
* Added an 'M' token to move multiple indexed joints to angles (ASCII format entered in the serial monitor) simultaneously;
* Re-arranged the IR keymap for the new customized IR panel.

## Jun 29, 2021
* OpenCat.ino will print out the model name (Bittle/Nybble) at booting up.
* Moved #define I2C_EEPROM to the beginning OpenCat.h.

## Jun 7, 2021

* Adjusted the threshold voltage so that Bittle will keep beeping when the battery goes under 6.5V, a few moments before the battery power shuts off;
* Adjusted the gaits so that the elbow won't hit the body in the accelerated phase. 
* The trot on key "1" is tuned to be faster.
* Removed the running gait on the IR remote key "2" and replaced it with "check around" behavior previously on key "3";
* Assigned a "play dead" trick to IR remote key "3". Bittle will fall on its back then roll back (if the gyro is activated);
* Removed the behavior when the robot is tilted at a large angle to avoid an occasional bug. Will put the behavior back if the bug can be fixed; 
* Added an auto-detection code for a new sound&light sensor connected to the analog Grove pin. Some new automated behaviors are being developed. The code block won't be active if the sensor is not connected to the Analog Grove socket;

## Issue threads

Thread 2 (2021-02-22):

OpenCat.ino Sketch to big to compile

loeweh, 2021-02-22:
Hi,

downloaded OpenCat.ino. It does not compile. Error is:

Sketch uses 33764 bytes (104%) of program storage space. Maximum is 32256 bytes.
Global variables use 1344 bytes (65%) of dynamic memory, leaving 704 bytes for local variables. Maximum is 2048 bytes.
Sketch too big; see http://www.arduino.cc/en/Guide/Troubleshooting#size for tips on reducing it.

Updated libraries to the latest.

Any idea?

BR Heiko

borntoleave, 2021-02-22:
You need to download version 2.6.1 of the IRremote library and set the
unused encoders to 0s.
More detailed instructions are mentioned in chapter 4 of the user manual at
bittle.petoi.com.

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

--
~~
Rongzhong Li, PhD
http://borntoleave.github.io

regularfry, 2021-02-24:
Can we get this documented in the Nybble guide too, please?  This affects the v0_2 board I've got too.

borntoleave, 2021-02-25:
Yes, it's already mentioned in the manual: https://nybble.petoi.com/chapter4#4-2-1-install-through-the-library-manager

ukkuroda, 2021-03-14:
For IR remote comes with biddle,
 only "DECODE_NEC", "DECODE_HASH" set to 1 and others set to 0.
You can find it in the image.
The document says "set unused decoders to 0" but there's no way to tell that the remote sends NEC codes.

borntoleave, 2021-03-15:
In the manual, there's a screenshot showing only the "DECODE_NEC" and
"DECODE_HASH" are set to 1, and others set to 0.
I'll add a sentence to explicitly indicate that.

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

--
~~
Rongzhong Li, PhD
http://borntoleave.github.io

kkiyama117, 2021-09-24:
Same error occured in my environment with the latest version of opencat.
Sketch uses 32448 bytes and global variables uses 1208 bytes.
What can I do to solve this issue?

borntoleave, 2021-09-24:
When did you download the code?
5 days ago I included the modified IR library in the OpenCat folder. You no
longer need to modify any files to get the code compiled and the flash
usage will be about 89%.

On Fri, Sep 24, 2021 at 11:41 AM kkiyama117 ***@***.***>
wrote:

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

--
~~
Rongzhong Li, PhD
http://borntoleave.github.io

kkiyama117, 2021-09-24:
I downloaded opencat yesterday, and do as　written in [docs](https://bittle.petoi.com/4-configuration).
 I haven't downloaded IRremote and also edited any files in opencat folder
Please tell me where I should check, because maybe I'm wrong. It seems
writeinstinct.ino works well.

borntoleave, 2021-09-24:
Did you start from a clean Arduino installation? Do you have some older
libraries installed previously?

On Fri, Sep 24, 2021 at 12:36 PM kkiyama117 ***@***.***>
wrote:

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

--
~~
Rongzhong Li, PhD
http://borntoleave.github.io

kkiyama117, 2021-09-24:
Since it's my first time using Arduino IDE, no libs should be installed but I'm going to try to reinstall everything. (I don't have time today, so I'll report back if it doesn't work.)

kkiyama117, 2021-09-25:
Reinstalling doesn't work well for me.
I'm using
- Arduino IDE 1.8.16 (installed by Pacman, installer of Manjaro Linux)
- [this version of I2Cdevlib](https://github.com/jrowberg/i2cdevlib/tree/c8e05299df44a974d0df07eb4b1a7b5893640ace)
- PWM Servo driver Library 2.4.0
- QList 0.6.7
- main branch of OpenCat

And the error occurs in compiling. I can't copy logs directly since I'm using Japanese translation, but it says
```
Sketch uses 32448 bytes (100%) of program storage space. Maximum is 32256 bytes.
Global variables use 1208 bytes (58%) of dynamic memory, leaving 840 bytes for local variables. Maximum is 2048 bytes.
text section exceeds available space in board
Sketch too big; see https://support.arduino.cc/hc/en-us/articles/360013825179 for tips on reducing it.
```

borntoleave, 2021-09-25:
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

Which board are you selecting? Are you choosing Arduino Uno?

kkiyama117, 2021-09-25:
I'm using version 1.0, and I choose Arduino Uno also.

kkiyama117, 2021-09-25:
I got it with using Arduino avr boards not with downloaded default by Arch Linux but with installed manually. Thanks for providing 　the beneficial support.

Closed 2021-03-24.

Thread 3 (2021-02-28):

Nybble - Adding new skill: need to move zero from EEPROM to PROGMEM

Troy-Chard, 2021-02-28:
Not sure if this is a bug or not, but thought I'd mention and let you decide :)

Last night, while trying to write custom zero skill for Nybble, it didn't seem to work.

The fix was easy: in my local branch, inside InstinctNybble.h:
1. I moved zero to progmemPointer[] array.
1. Revised it to "zeroN" in skillNameWithType array.
1. Re-ran WriteInstinct.ino to update the skills
1. Ran and uploaded my OpenCat.ino copy.

And to gain a bit more space in Program memory I commented out hs, hs1, hs2 skills.

Now, I can just tweak the zero skill and upload the code... no need to re-run WriteInstinct.  But I needed it the first time just to move zero out of EEPROM and into Program memory (if I understand right).

borntoleave, 2021-03-01:
It relates to the memory location to save a skill. The code posted on
GitHub should have the right settings. Do you have a screenshot showing
the codes that don't work? Was it identical to the raw GitHub code?

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

--
~~
Rongzhong Li, PhD
http://borntoleave.github.io

Troy-Chard, 2021-03-01:
It could be what's in the repo is correct as is :)

I just noticed that, before I could use the zero skill myself to try a new behaviour, I needed to add an entry to the [progmemPointer array in InstinctNybble.h](https://github.com/PetoiCamp/OpenCat/blob/9571607df11fe6ecb07a70122fb2792cdd7a202e/WriteInstinct/InstinctNybble.h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).

( I saw the [progmemPointer already has it in InstinctBittle.h](https://github.com/PetoiCamp/OpenCat/blob/9571607df11fe6ecb07a70122fb2792cdd7a202e/WriteInstinct/InstinctBittle.h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) )

Also I revised the name in the [skillNameWithType](https://github.com/PetoiCamp/OpenCat/blob/9571607df11fe6ecb07a70122fb2792cdd7a202e/WriteInstinct/InstinctNybble.h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
) array to be "ZeroN" instead of "ZeroI"  ( following the example in InstinctBittle.h )

( But then OpenCat.ino got too big, so I commented out hs, hs1, hs2, entries ).

After editing my skill a few times and uploading, it didn't seem to work though (it just kept doing similar to calib pose iirc).

Then I realized I needed to run WriteInstinct.ino to rewrite the EEPROM with new settings moving zero from EEPROM to PROGMEM 💡 and then my zero Newbility worked :)

The new entries in my copy here appear as:
```
#if !defined(MAIN_SKETCH) || !defined(I2C_EEPROM)
		//if it's not the main sketch to save data or there's no external EEPROM,
		//the list should always contain all information.
  const char* skillNameWithType[]={"bdI","biI","bkI","bkLI","bkRI","crFI","crLI","crRI","lyI","trFI","trLI","trRI","vtI","wkFI","wkLI","wkRI","balanceI","buttUpI","calibI","droppedI",/*"hsN","hs1N","hs2N",*/"liftedI","luI","restI","sitI","sleepI","strI","zeroN","hiI","peeI","puI","rcI",};
  const char* progmemPointer[] = {bd, bi, bk, bkL, bkR, crF, crL, crR, ly, trF, trL, trR, vt, wkF, wkL, wkR, balance, buttUp, calib, dropped, /*hs, hs1, hs2,*/ lifted, lu, rest, sit, sleep, str, zero, hi, pee, pu, rc, };
#else	//only need to know the pointers to newbilities, because the intuitions have been saved onto external EEPROM,
	//while the newbilities on progmem are assigned to new addresses
  const char* progmemPointer[] = {/*hs, hs1, hs2,*/ zero, };
#endif
```

( and this is just me fooling around trying my first newbility... really I should maybe be writing my own .ino. eventually :P

Troy-Chard, 2021-03-01:
( more background ... )

My Newbility is sad so far though...
```
const char zero[] PROGMEM = {  // turtle roll?   ( it's not even close yet :(
-5, 0, 0, 1,
 0, 0, 0,
  -10,-100,   5,   0,   0,   0,   0,   0,  80,  80, -80, -80, -55, -55,  55,  55,   8, 10, 0,0, // tuck
    0,  10,   5,   0,   0,   0,   0,   0,  84,  84,  80,  80,  90,  90, -90, -90,   2, 4,  0,0,  // arch
   70,  10,   5,   0,   0,   0,   0,   0, -90,   0,   0,  90,  90,  90, -90, -90,   9, 2,  0,0,  // roll - speed 100 should cause movement in one step, but, wow, hard on the servos :(
  -70,  40,   5,   0,   0,   0,   0,   0,   0, -90,  90,   0,  90,  90, -90, -90,  30, 6,  0,0,  // Flip.A
    0,   0,   0,   0,   0,   0,   0,   0,  30,  30, -30, -30,  30,  30, -30, -30,   2,20,  0,0, // stand?
};
```

But my Nybble has protective gear to handle testing which I can peel off later pretty easy :)

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

borntoleave, 2021-03-01:
Oh, yes, thanks for reporting. I have added zero back to the newbility list
and also updated the data structure of Nybble behaviors for the new code.

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

--
~~
Rongzhong Li, PhD
http://borntoleave.github.io

Troy-Chard, 2021-03-01:
Thanks RZ! :)

borntoleave, 2021-03-02:
Have you disabled the unused encoders in IRremote.h? It's about 85% after compiling on my side.

Troy-Chard, 2021-03-02:
I'll try that, thanks!

The problem I noticed with sketch size is in the current main branch of OpenCat :(
I just don't want people trying Nybble for the first time to hit the problem.  ( sorry for the troubles my change request is causing 😮 )

borntoleave, 2021-03-02:
If you disable the unused encoders in IRremote.h, it will save about 10%
space.
I verified the compiling result on my end:
*Bittle*
Sketch uses 28374 bytes (87%) of program storage space. Maximum is 32256
bytes.
Global variables use 1198 bytes (58%) of dynamic memory, leaving 850 bytes
for local variables. Maximum is 2048 bytes.
*Nybble *
Sketch uses 28244 bytes (87%) of program storage space. Maximum is 32256
bytes.
Global variables use 1202 bytes (58%) of dynamic memory, leaving 846 bytes
for local variables. Maximum is 2048 bytes.

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

--
~~
Rongzhong Li, PhD
http://borntoleave.github.io

Troy-Chard, 2021-03-02:
Thanks borntoleave, that's great :)

Troy-Chard, 2021-03-04:
Quick follow-up... 85% is what I get too.  Thanks again borntoleave :)

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

Closed 2021-03-02.

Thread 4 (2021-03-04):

Incorrect servos behavior in calibration mode

MrDobert, 2021-03-04:
Robot still reading the body angle and try to rebalance if it's over a safe angle in calibration mode. Reference: [Servos move in calibration mode](https://www.petoi.com/forum/basic-assembly-and-setup/servos-move-in-calibration-mode)

borntoleave, 2021-03-24:
I have disabled the gyro in calibration mode in the last update. But you will need to turn on the gyro after exiting the calibration mode.

Closed 2021-03-24.

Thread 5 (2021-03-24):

WriteInstinct Missing Dependency

Kenttleton, 2021-03-24:
Under the WriteInstinct.ino is missing the Adafruit_PWMServoDriver.h file referenced in OpenCat.h. I was able to track down the library this is from but it should either be included or at least documentation on where to get the library would be helpful.

Cosmosauras, 2021-03-24:
Doc is here:

https://bittle.petoi.com/4-configuration

borntoleave, 2021-03-24:
I added the link to the [documentation center](https://docs.petoi.com) in Readme.

Closed 2021-03-24.

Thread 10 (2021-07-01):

when upload OpenCat.ino the monitor stop with the following content

gst6062825, 2021-07-01:
* Start *
Initialize I2C
Connect MPU6050
Test connection
MPU successful
Initialize DMP
901 96 -36 87
Enable DMP
Enable interrupt
DMP ready!

* Assigning 1 skill addresses...

gst6062825, 2021-07-01:
I've fixed the problem of using different baud rates to upload the WriteInstinct.ino and OpenCat.ino

Closed 2021-07-01.

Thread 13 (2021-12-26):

Understanding the format of a behavior: trigger axis

durka, 2021-12-26:
The `bf` behavior is defined as: https://github.com/PetoiCamp/OpenCat/blob/f1013cece692d6ff9d86577a7216416f9587aa2d/WriteInstinct/InstinctBittle.h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

If I understand correctly, the fifth frame is triggered by a pitch angle of -10 degrees. The sixth frame seems to have the trigger axis set to zero (i.e. no trigger axis) but there is an angle value. It seems that the `127` will never be read because the axis is tested first and you can't trigger on yaw: https://github.com/PetoiCamp/OpenCat/blob/f1013cece692d6ff9d86577a7216416f9587aa2d/OpenCat.ino#L740-L742

Is this meant to be ignored, or an error, or do I misinterpret the format?

borntoleave, 2021-12-26:
The parameters for the bf (backflip) skill may be different for each model
due to the inconsistency of many factors, like calibration and surface
friction. As far as I tested on my end, most of the models can complete a
backflip. Since you may need to tune the parameters by yourself, I just
left a few non-functional residues during experiments as is.

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

--
~~
Rongzhong Li, PhD
http://borntoleave.github.io

durka, 2021-12-26:
OK, so indeed that 127 doesn't do anything but doesn't hurt anything by being there. Thanks for confirming!

Closed 2021-12-26.

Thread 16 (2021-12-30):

New serial code doesn't work with RPi hat

sskorol, 2021-12-30:
Hi @borntoleave @JasonWong08,

I noticed a recent update in serial code. Wondering if you have tested it with an RPi hat?

It doesn't work for me. First of all, it incorrectly detects a serial port: `/dev/ttyAMA0` is wrong for RPi. There should always be `ttyS0`.

I updated it manually in code, but serial behavior still seems incorrect to me:

- Some commands work, the others - not. E.g. I can run `ksit`, but further `kbalance` doesn't work or vice versa.
- NyBoard is always stuck after 1 or 2 commands and requires a reset.
- Sometimes I see response parsing exceptions for the correct commands, e.g. [here](https://github.com/PetoiCamp/OpenCat/blob/main/serialMaster/ardSerial.py#L155) when we try to extract a 0-element from empty object.
- NyBoard is totally unstable: it may beep several times before or after the command's execution but there's no response at all.

Note that I can still control Bittle with IR until the board is stuck on serial.

I can record a video of course. But it's not really helpful when the board is stuck in 1 command and Bittle becomes unresponsive.

Any thoughts or comments on how to make the serial interface stable with an RPi hat would be greatly appreciated.

#### Hardware / Environment

- Bittle / NyBoard_V1_0
- RPi Zero 2W / model A+
- x64 Ubuntu 20.04

JasonWong08, 2022-01-01:
@sskorol Thank you for your committing the issue. we have done a workaround to fix it.

borntoleave, 2022-01-04:
We have added a logic to automatically select the Pi's port when it's connected directly through the 2x5 socket (not through USB). You can still manually define the port if the automatic logic doesn't work in your case.

We tested the script on Raspian. We didn't observe other problems you mentioned in your issue. The script can keep taking serial commands until you enter "q" or "quit".

Please let us know if you have more problems, or is it ok to close this issue.

sskorol, 2022-01-04:
Ok, thanks, I'll test it today.

sskorol, 2022-01-05:
@borntoleave @JasonWong08 I tested the new code and still see the same issues. I recorded the video with mostly all of them: https://youtu.be/v-gfkdAKLus

sskorol, 2022-01-05:
I have a quick update. Just googled issues with RPi serial port. Found the following thread: https://raspberrypi.stackexchange.com/questions/114366/rpi4-serial-port-not-working-on-either-raspberry-os-or-ubuntu

I followed all the steps from the answer and now the serial port works as expected. I tried different commands. There are no hangings or weird movements anymore. Most likely there were some serial interruptions with integrated BT, as I noticed a `dtoverlay` in my boot config + there was a `python-serial` installed via apt.

Anyway, it's worth copy-pasting the following instructions to your official docs for all the users that may face similar issues with RPi hats:

- add `enable_uart=1` to `/boot/config.txt`
- remove `console=serial0,115200` from `/boot/firmware/cmdline.txt` on Ubuntu and `/boot/cmdline.txt` on Raspberry Pi OS
- disable the serial console: `sudo systemctl stop serial-getty@ttyS0.service && sudo systemctl disable serial-getty@ttyS0.service`
- make sure you have `pyserial` installed if you're using the python serial library, not python-serial from apt.
- create the following udev file (I created `/etc/udev/rules.d/50-tty.rules`):
```
KERNEL=="ttyS0", SYMLINK+="serial0" GROUP="tty" MODE="0660"
KERNEL=="ttyAMA0", SYMLINK+="serial1" GROUP="tty" MODE="0660"
```
- reload your udev rules: sudo udevadm control --reload-rules && sudo udevadm trigger
- change the group of the new serial devices:
```
sudo chgrp -h tty /dev/serial0
sudo chgrp -h tty /dev/serial1
```
- The devices are now under the tty group. Need to add the user to the tty group and dialout group:
```
sudo adduser $USER tty
sudo adduser $USER dialout
```
- update the permissions for group read on the devices:
```
sudo chmod g+r /dev/ttyS0
sudo chmod g+r /dev/ttyAMA0
```
- reboot

sskorol, 2022-01-05:
BTW, here's what I get from `platfrom.uname()` in Python on RPi / Ubuntu:
```
uname_result(system='Linux', node='rpi', release='5.4.0-1047-raspi', version='#52-Ubuntu SMP PREEMPT Wed Nov 24 08:16:38 UTC 2021', machine='aarch64', processor='aarch64')
```

JasonWong08, 2022-01-05:
@sskorol, Great! You got the key! you can refer to my post on OpenCat Forum about how to solve this issue (https://www.petoi.camp/forum/software/fixed-the-issue-on-github-new-serial-code-doesn-t-work-with-rpi-hat-16).
actually we use the serial port - **/dev/ttyS0**
So on your side, you can modify the script simply like this:
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
Please have a try again and feel free to contact us. Thanks a lot.

JasonWong08, 2022-01-05:
For raspberry Pi hard hardware, if you plug it in Nyboard,  We actually use **/dev/ttyS0**. No matter what operating system you installed (Ubuntu or Raspbian etc.), you should enable it at first.
If you installed Raspbian, you can refer to the Section 4.4.1. (Config Raspberry Pi serial port) in the user manual
https://bittle.petoi.com/4-configuration

If you installed Ubuntu, you can refer to @sskorol 's comment above.

sskorol, 2022-01-05:
> @sskorol, Great! You got the key! you can refer to my post on OpenCat Forum about how to solve this issue (https://www.petoi.camp/forum/software/fixed-the-issue-on-github-new-serial-code-doesn-t-work-with-rpi-hat-16). actually we use the serial port - **/dev/ttyS0** So on your side, you can modify the script simply like this: 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 Please have a try again and feel free to contact us. Thanks a lot.

@JasonWong08 @borntoleave if you take a look at the above comments and video, you'll notice that there was no problem for me to change a port in a code. The issue I highlighted is about the actual fact that `platform.uname()[1] == 'raspberrypi'` you use for automatic `ttyS0` assignment in a script doesn't work on Ubuntu/RPi (see the output of a https://github.com/PetoiCamp/OpenCat/issues/16#issuecomment-1005307333).

JasonWong08, 2022-01-05:
@sskorol, thank you for your advice. We'll fix it in a better way.

Closed 2022-10-25.

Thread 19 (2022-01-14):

Bittle sometimes doesn't physically respond to Serial commands

sskorol, 2022-01-14:
**Robot**: Bittle
**Hardware**: NyBoard v1.0, RPi Zero 2 W
**Software**: Ubuntu Server 20.04, Python 3.8

**Steps**:
1. Run `ardSerial.py`
2. Send **kbalance** command
3. Send **krest** command
4. Send **kbalance** command
5. Send **krest** command

**Expected**: all the commands are successfully executed, Bittle performed the requested actions.
**Actual**: the last `krest` is executed, but Bittle didn't perform any action.

Check the [video](https://youtu.be/CsW0uFY08yg) to see it in action.

Note that it's not related to `krest` command only. I observed the same behavior for any command. Everything may work smoothly, and then in a moment, some command is just skipped.

Also note that seems like I'm not alone here. I investigated existing GitHub repos for Bittle and found [this one](https://github.com/EnriqueMoran/BittleXboxController) for the gamepad teleop.  There's a list of know issues at the end.

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

The second one seems very close to what I'm talking about. And this repo uses [pyBittle](https://github.com/EnriqueMoran/pyBittle) library as a dependency for Serial communication.

Anyway, it seems like there's a bug. So would be greatly appreciated if you can take a look @borntoleave @JasonWong08.

Thanks,
Sergey

borntoleave, 2022-01-16:
There seems to be a bug in the motion code when loading skills. I tried to
find it but was not successful. I'll give it another try this month.
Before that, you may try sending the command twice or send it right after
"balance"?

On Sat, Jan 15, 2022 at 4:39 AM Sergey Korol ***@***.***>
wrote:

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

--
~~
Rongzhong Li, PhD
http://borntoleave.github.io

sskorol, 2022-01-16:
@borntoleave it'd probably work. But the main logical issue here is that each skill behaves like an infinite loop of repetitive operations. In this case, we always want to prevent redundant commands sending (aka duplicates) by checking what was the last action. Otherwise, teleop tools that are designed to constantly send the recent state would just DDOS the Bittle. And that's why in the most of implementations people add an additional protection to serial code e.g. `if current_command != previous_command`. That's what I did as well. Yeah, I can still send the command twice if I want. But the things might become much easier if apart from the skills there will be implemented a more common for ROS technic, when we move objects based on (x, y, z, th) vectors. Then I can constantly send just coordinates's updates, and Bittle would decide how to reach those points.

sskorol, 2022-01-16:
BTW, can you provide a pattern for a single "step"? E.g. when we walk or crawl, such skills consist of a number of repetitive steps I guess. I want to extract it for testing.

borntoleave, 2022-01-16:
> BTW, can you provide a pattern for a single "step"? E.g. when we walk or crawl, such skills consist of a number of repetitive steps I guess. I want to extract it for testing.

Yes, in instinctBittle.h, you can find the frames of gaits. The explanation of the format can be found at https://bittle.petoi.com/11-tutorial-on-creating-new-skills.

sskorol, 2022-01-16:
@borntoleave I checked the guide but it's not really clear what are 1-7 joint angles for in the provided table? And what would happen if I change 1-7 values while calibration?

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

Moreover, I see that we can set the head's angle for static postures. But it's missing for gaits. Can you elaborate on that? And how can I control it? If we talk about camera usage, I'd prefer disabling the head's rotation while moving, as RPi can't stabilize the video and streaming becomes awful.

sskorol, 2022-01-17:
Seems like I found where the head is controlled in code: https://github.com/PetoiCamp/OpenCat/blob/main/OpenCat.ino#L828-L833

But it's not really convenient that I need to disable it globally. Would be great to have some option probably to have more flexible head control.

P.S. The question regarding 1-7 joint angles is still actual.

borntoleave, 2022-01-17:
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

The 1~7 joints are reserved for our 12 DOF robot, with head, tail, and should roll angles.

The joints are grouped by four for the convenience of logic conditions in the code:

|                  |                  |                  |                  |
|------------------|------------------|------------------|------------------|
| head pan,        | head tilt        | tail pan         | N/A              |
| shoulder roll 1  | shoulder roll 2  | shoulder roll 3  | shoulder roll 4  |
| shoulder pitch 1 | shoulder pitch 2 | shoulder pitch 3 | shoulder pitch 4 |
| knee pitch 1     | knee pitch 2     | knee pitch 3     | knee pitch 4     |

Gaits use periodical data. If I include the head and unused joints' angles (0-7 joints), it will double the flash memory usage and exceed the available SRAM on ATmega328P. So for the 8 DOF models, I only save 8 joints (8-11 joints) per frame for the gaits. The postures and behaviors have only one frame or a few frames, so I kept all the joints for better compatibility for my future models. Changing the calibration value of 1-7 joints won't affect anything because no servos are attached to those ports.

The head movement is generated on the fly as a function of the period of the gait. It's a trade-off for limited flash space. The good part is that you may adjust the amplitude and period of the rotation to compensate for the wobbling of the body.

sskorol, 2022-01-17:
Ok, thanks for clarification! I'll play with head's rotation.

Let me know when you find the root cause of the original issue with serial commands please.

borntoleave, 2022-03-17:
Hi,
I have fixed the issue and pushed a big update to the firmware: https://github.com/PetoiCamp/OpenCat/tree/2.0
You can read the changelog for the major updates: https://github.com/PetoiCamp/OpenCat/blob/2.0/ChangeLog.md

sskorol, 2022-03-17:
Hi, thanks for the update. Unfortunately, I can't check it at the moment. You know what happens in Ukraine. Bittle is waiting at home until the war is over.🇺🇦

JasonWong08, 2022-03-18:
> Hi, thanks for the update. Unfortunately, I can't check it at the moment. You know what happens in Ukraine. Bittle is waiting at home until the war is over.🇺🇦

Take care bro.

borntoleave, 2022-04-14:
Fixed in the 2.0 branch

Closed 2022-04-14.

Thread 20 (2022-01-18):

Getting IMU data

sskorol, 2022-01-18:
Hi @borntoleave,

Is it possible to retrieve IMU data from Bittle programmatically? I want to get odometry for SLAM package integration.

Thanks,
Sergey

borntoleave, 2022-01-18:
You can delete the macro for DEVELOPER, and use the code blocks inside to print out the angles. The format is yaw, pitch, roll.

```c
#ifdef FIX_OVERFLOW
      for (byte g = 1; g < 3; g++) {
        yprLag[lag][g] = ypr[g];
        ypr[g] = yprLag[(lag - 1 + HISTORY) % HISTORY][g] ;
      }
      lag = (lag + 1) % HISTORY;
#endif

#ifdef DEVELOPER
      PT(ypr[0]);
      PTF("\t");
      PT(ypr[1]);
      PTF("\t");
      PTL(ypr[2]);
#endif
    }

sskorol, 2022-01-18:
@borntoleave and what about coordinates? I guess they are stored in `gravity` vector?

borntoleave, 2022-01-18:
If you look at the testMPU.ino in the ModuleTest folder, you can see how to print out the x y z values.

Sent from my iPhone

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

sskorol, 2022-01-18:
@borntoleave great, thank you!

sskorol, 2022-01-22:
@borntoleave to provide sufficient info to nav package I need to collect linear acceleration, angular velocity and orientation from IMU. Just want to confirm this info can be collected from Bittle. I see several examples with accel, but not really sure what’s the difference between common accel and world accel? I also see quaternion structure in code. Is it sufficient to determine orientation? Or I need to apply additional formulas against pitch, roll and yaw to compute it? And for angular velocity I guess I can use roll, pitch and yaw, right?

borntoleave, 2022-01-22:
The MPU6050 code is cited from this project:
https://github.com/jrowberg/i2cdevlib/tree/master/Arduino/MPU6050

The ypr from the code is yaw, pitch, roll angles, not velocities. You
always measure acceleration then integrate to get the velocity and
position.

If you plot the common accel and world accel and see their feedback with
your motion, you can compare the differences and decide the best one. I'm
using aaWorld for my experiments.

On Sat, Jan 22, 2022 at 8:03 AM Sergey Korol ***@***.***>
wrote:

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

--
~~
Rongzhong Li, PhD
http://borntoleave.github.io

sskorol, 2022-01-25:
@borntoleave I want to try another IMU (10 DOF). However, i2c port on RPi is occupied by the NyBoard. Can I access NyBoard's i2C from RPi if I solder the sensor's pins to the available slots above the i2c groove socket?
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

borntoleave, 2022-01-25:
In short, yes. As long as you keep the I2C switch on Arduino, the I2C port
of RPi is dangling. You can connect external sensors to its port. You need
to keep the magnetic sensors away from the body to avoid interference by
the servos' motion because the servos emit very strong EM fluctuation.

If you dial the I2C switch from Arduino to RPi. The I2C grove and all the
devices on I2C will be taken over by the RPi. However, the servo driver
PCA9685 will also be controlled by RPi, and the motion pattern generator
ATmega328P won't be in effect.

On Tue, Jan 25, 2022 at 9:15 AM Sergey Korol ***@***.***>
wrote:

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

--
~~
Rongzhong Li, PhD
http://borntoleave.github.io

sskorol, 2022-01-25:
> You can connect external sensors to its port.

Do you mean RPi port or those i2C port linked with a groove?
RPi port is already occupied with a hat. I just need to access an external i2C sensor via RPi.

Are you saying it's possible only if RPi switch is on?

borntoleave, 2022-01-25:
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
As long as the I2C switch is not dialed at RPi, the I2C port of RPi is not really connected to the board's I2C network.
The switch can disconnect the I2C network from 328P and connect them to the RPi.

sskorol, 2022-01-25:
@borntoleave but even if it's not connected to NyBoard's i2c network, the RPi pins would still be occupied if we use Zero or A+ board as a hat. So we can't physically connect sensors directly to Pi's i2c. And if a switch the I2C network from 328P, I won't be able to control servos via OpenCat code anymore, as you have mentioned. So what would be your recommendation in this case? What's the best option of connecting i2c sensor to Pi mounted on top of 328P w/o loosing the main functionality.

borntoleave, 2022-01-25:
You can jump four wires between your sensor and the Pi: Vcc, GND, SCL, and
SDA.
Pay attention to the voltage level of Vcc, SCL, and SDA. The voltage level
of SCL and SDA on Pi is 3.3V.
For Vcc, you can choose either 3.3V or 5V from Pi to fit your sensor's
needs.

On Tue, Jan 25, 2022 at 10:41 PM Sergey Korol ***@***.***>
wrote:

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

--
~~
Rongzhong Li, PhD
http://borntoleave.github.io

sskorol, 2022-01-25:
But SCL and SDA pins are occupied by NyBoard when Pi is used as a hat. And 2 extra SCL/SDA pins on Pi are intended to eeprom usage only. They won't work for common use cases. So how can I wire SDA/SCL between Pi (connected to NyBoard) and a sensor then?

borntoleave, 2022-01-25:
> SCL and SDA pins are occupied by NyBoard (2x5 socket) when Pi is used as a hat.

Yes.  But they are not really connected to anything devices. So you can solder two wires to the back of the pins on the Pi.

sskorol, 2022-01-29:
@borntoleave well, I did it, but here's a new issue. When I run `i2cdetect -y 1`, it gives me the following picture:

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

By default, if don't connect RPi to NyBoard, I have only a single 68 address occupied by my sensor. But the RPi is used as a hat, I see this weird matrix. 68 address doesn't work anymore. How can I guess which one is mine now w/o brute-forcing each address? I'm also wondering why all those addresses are occupied. Is NyBoard really bind them for something?

sskorol, 2022-01-29:
Ok, from the above picture I see that 0x68 address is used by MPU6050. So that's a problem. 2 sensors have the same address. Any thoughts on how to resolve this conflict?

sskorol, 2022-02-07:
Made it work via software i2c bus. Details here: https://forums.raspberrypi.com/viewtopic.php?p=1968858#p1967861

@borntoleave I see you committed accel data printing feature. Have you also tried to output raw gyro data? I played with it a bit based on the provided samples but always got constant values like [0;0;1]. Also, wondering why there are int values and not float like for accel?

borntoleave, 2022-02-08:
Thanks for the note on I2C.

The IMU code is mostly from [i2cdevlib](https://github.com/jrowberg/i2cdevlib/blob/master/Arduino/MPU6050/examples/MPU6050_DMP6_using_DMP_V6.12/MPU6050_DMP6_using_DMP_V6.12.ino). The raw gyro data is **VectorInt16 gy** and you may print it out similar to the example code. 

The accel data is read from the register and is in integer type. You may divide some factors to get real accelerations in float. 

I validated the updated code again on my board. The 'v' token prints the MPU data once and the 'V' token prints the MPU data for every loop. I got the readings changed with my movements.

sskorol, 2022-02-08:
@borntoleave what lib/tool do you use for plotting real-time data?

borntoleave, 2022-04-14:
The 2.0 branch has a switch case for printing gyros. token -v and -V

Closed 2022-04-14.

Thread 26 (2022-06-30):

Please make a stable release

ImFstAsFckBoi, 2022-06-30:
@borntoleave Since this repo is so frequently updated our code sometimes break when you push a new commit. It would be great if you could make a stable release.

ImFstAsFckBoi, 2022-07-01:
This particular time the 15 second delay added to the readSignal loop blocked all sensor data and caused some issue for us. Not sure which commit we used before, I think it was from 2.0 before it was merged with main. If you keep main untouched that would be fine but best would be if you also archived every major update as a GitHub release. Eitherway, thank you.

Closed 2022-07-01.

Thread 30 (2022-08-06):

Is it possible to remote-control precise Bittle gaits?

slerman12, 2022-08-06:
I've seen examples such as pyBittle of sending pre-programmed gaits to the Bittle via WiFi or Bluetooth. I'm an AI researcher looking to instead send precise velocities and torques to the Bittle for exact joint control. I also need to capture the Bittle's accelerometer and gyroscope data.

Is there example code anywhere for how to achieve both of these goals?

1. Send precise commands
2. Receive Bittle metadata

Thanks for any help!

borntoleave, 2022-08-07:
Hi,
1. Bittle's servo moves by position control. You can send interpolated
positions at different time intervals to tune the velocities. Our official
example can be found in serialMaster/example.py.

2. In OpenCat.h, you can uncomment
#define T_PRINT_GYRO            'v' //print Gyro data
#define T_VERBOSELY_PRINT_GYRO  'V' //verbosely print Gyro data
and send 'v' or 'V' to get the IMU data. The current code only sends gyro
data, but you can print the full 6-axis data (including the acceleration)
by modifying the print6Axis() function in OpenCat/src/imu.h.

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

--
~~
Rongzhong Li, PhD
http://borntoleave.github.io

slerman12, 2022-08-07:
Oof, this may be beyond my expertise.

I'm gonna really need your input if I'm to do this.

Okay, I've looked at `example.py`.

> You can send interpolated positions at different time intervals

1. Is there a line in `example.py`  that sends a "position"? I'm not sure what is meant by this.
2. Is it possible to send positions via Bluetooth or WiFi? There is a library called pyBittle that makes sending commands to Bittle via Bluetooth/WiFi really easy, but they only by default send full pre-programmed gaits.

I've taken a look at `opencat.h` and `imu.h`, but this is where I really don't have the expertise since I don't program outside of Python often.

> you can print the full 6-axis data (including the acceleration) by modifying the print6Axis() function in OpenCat/src/imu.h

1. I see the following code in `imu.h`. How can I modify it to output accelerometer data in addition to gyroscope data? Any hints?

```
void print6Axis() {
  PT(ypr[0] );
  PT('\t');
  PT(ypr[1] );
  PT('\t');
  PT(ypr[2] );
  PTL();
}
```

2. Is it possible to receive these print signals via Bluetooth or WiFi?

Thank you so much!

borntoleave, 2022-08-09:
1. In OpenCat/serialMaster/demos, you can find an example moveBySteps.py that moves specific joints by time intervals.
2. Yes, you can connect the Bluetooth dongle to your computer and then run any of the examples that import the ardSerial.py. There's an algorithm in the code that automatically detects connected robots.
3. To get more IMU data, simply uncomment the lines after print ypr[]
```c++
void print6Axis() {
  PT(ypr[0] );
  PT('\t');
  PT(ypr[1] );
  PT('\t');
  PT(ypr[2] );
  PT("\t");
  PT(aaWorld.x);
  PT("\t");
  PT(aaWorld.y);
  PT("\t");
  PTL(aaWorld.z / 1000);
  PT('\t');
  PT(aaReal.z);
  PTL();
}

```

If you send a 'v' token, the angles will be printed to the serial port for once. And the Bluetooth or WiFi dongle can transfer it to your computer. If you send a 'V' token, the angles will be continuously printed to the serial port.

Currently, the Bluetooth code is fully incorporated in the ardSerial.py.

slerman12, 2023-02-09:
Hi Rz, this is Sam. Currently, I'm testing Bluetooth bidirectional commands. Here is the output when I send the following command:

`b'v'`

```
0000ffe1-0000-1000-8000-00805f9b34fb (Handle: 15): Vendor specific: bytearray(b'G\r\n-21.26759\t10.8250')
0000ffe1-0000-1000-8000-00805f9b34fb (Handle: 15): Vendor specific: bytearray(b'7\t-11.13954\r\nv\r\n')
```

Here is the output when I send the following command:

`b'k'`

```
0000ffe1-0000-1000-8000-00805f9b34fb (Handle: 15): Vendor specific: bytearray(b'G\r\n')
0000ffe1-0000-1000-8000-00805f9b34fb (Handle: 15): Vendor specific: bytearray(b'k\r\n')
```

In this case, Bittle briefly moves his head.

Here is the output when I send the following command:

`b'-9'`

`0000ffe1-0000-1000-8000-00805f9b34fb (Handle: 15): Vendor specific: bytearray(b'G\r\n-\r\n')`

Bittle beeps, but nothing happens. (Same for other variations).

Can you show me how to send individual commands and bytearrays of commands? I'm using a special library because my M1 MacBook was having issues with the Bluetooth code.

slerman12, 2023-02-10:
This seems to work:

`str('m 0 45 0 -45 0 45 0 -45').encode('utf-8')`

But this doesn't:

`str('l 20 0 0 0 0 0 0 0 45 45 45 45 36 36 36 36').encode('utf-8')`

And neither does this:

`str('m 1 45 2 -45 3 45').encode('utf-8')`

Here is my best solution. Is there a better way than this that doesn't require calling `time.sleep(1)` and can automatically detect when a command has finished executing?

```
commands = list(map(encode, [[45, 0, 0, 0, 0, 0, 0, 0, 45, 45, 45, 45, 36, 36, 36, 36],
                             [-45, 0, 0, 0, 0, 0, 0, 0, 45, 45, 45, 45, 36, 36, 36, 36],
                             [45, 0, 0, 0, 0, 0, 0, 0, 45, 45, 45, 45, 36, 36, 36, 36],
                             [-45, 0, 0, 0, 0, 0, 0, 0, 45, 45, 45, 45, 36, 36, 36, 36]]))

def encode(rotations: list):
    return ('i ' + ' '.join(map(str, [*sum(zip(servos, rotations), ())]))).encode('utf-8')

def send(data):
    ...

for command in commands:
    # Send command via Bluetooth
    send(command)

    time.sleep(1)
```

borntoleave, 2023-02-10:
Hi, please download the latest OpenCat
<https://github.com/PetoiCamp/OpenCat> firmware on GitHub and upload it to
your Bittle. I just optimized the overall stability of the serial
communication. You can refer to the serialMaster/example.py for the
posture-related commands and the function to send them. Pay attention to
the brackets and letter cases.

            # - I indicates the command to rotate multiple joint servos at
the same time

            # - 8, 9, 10, 11, 0 indicate the index numbers of joint servos

            # - 50, 50, 50, 50, 0 indicate the rotation angle (this angle
refers to the origin,

            #                     rather than additive), the unit is degree

            # - 3 indicates the postponed time after finishing the command,
in seconds

            ['I', [8, -20, 0, 0, 9, -20, 10, 20, 11, 20, ], 1],

            ['I', [8, 20, 0, 40, 9,  20, 10, 50, 11, 50, ], 1],

            # - L indicates the command to control all joint servos to
rotate at the same time

            #     (currently the command supports 16 degrees of freedom,
that is, 16 servos)

            # - 20,0,0,0,0,0,0,0,45,45,45,45,36,36,36,36 indicate the
rotation

            #               angle of each joint servo corresponding to 0-15
(this angle refers to

            #               the origin, rather than additive), the unit is
degree

            # - 5 indicates the postponed time after finishing the command,
in seconds

            ['L', [20, 0, 0, 0, 0, 0, 0, 0, 5, 0, 45, 45, 80, 80, 36, 36], 1
],

For the 'I' commands, only 5 pairs of indexes and joint is allowed, making
the total length to 10. You may change the limit in OpenCat.h:
#define CMD_LEN 10 //the last char will be '\0' so only CMD_LEN-1 elements
are allowed

If you want to change more joints at once, the 'L' command encodes the
whole 16 joints and is more efficient.

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
slerman12, 2023-02-12:
Since I'm reading the IMU regularly, it's vital that I disable the beeping. Is it possible to send Bittle a command like `b'v'` soundlessly?

slerman12, 2023-02-12:
Is it possible to get IMU data _while_ Bittle is performing actions?

borntoleave, 2023-02-13:
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

slerman12, 2023-02-28:
I need to define constraints on Bittle's movements so that random actions don't cause him to twist a leg into his body or collide with himself. What are some of the red-zone ranges, do you know? Depending on where the other legs are, different movements are acceptable. So I may have to come up with this myself, but do you have an intuition for a general rule of thumb that can be used to constrain his movements depending on his other movements? In my scenario, he starts out taking random actions and this can be too demanding on the build.

borntoleave, 2023-03-05:
There's a simple rule to limit a single joint's range in OpenCat.h. 
```cpp
int angleLimit[][2] = {
  { -120, 120 }, { -30, 80 }, { -120, 120 }, { -120, 120 },
  { -90, 60 }, { -90, 60 }, { -90, 90 }, { -90, 90 },
  { -200, 80 }, { -200, 80 }, { -80, 200 }, { -80, 200 },
  { -80, 200 }, { -80, 200 }, { -80, 200 }, { -80, 200 },
};

You will need to calculate the exact legs' states to evaluate the collision with other body parts. The calculation could be done on the BiBoard or your master computer that sends the movement instructions. It's very challenging to fit that algorithm into NyBoard.

slerman12, 2023-06-23:
Hi Rz, I'm returning to this. Is it alright if I ask some questions that I stumbled into last time?

1. Reproducing the pre-programmed gaits via the kind of position control above seems... there seems to be something missing. I think the pre-programmed gaits have different velocities, right? I want to give the robot an action space from which it could feasibly learn to reproduce the pre-programmed gaits.
2. Are there any high-level examples of miniature movements like taking just _one_ step forward, or _one_ step to the right, etc.?
3. is it possible to disable the automatic trigger movements, like flipping upright when Bittle collapses. It's precisely this kind of movement that I have a hard time imagining the above action space reproducing.

Thank you.

borntoleave, 2023-06-24:
Hi,
Have you tried the SkillComposer
<https://docs.petoi.com/desktop-app/skill-composer>, which allows you to
import the entire instinct library and inspect each skill frame? You can
define the gait as a behavior and change the speed and loop cycles.
A skill data array can also be sent through the serial API
<https://docs.petoi.com/apis/python-api> so that you don't need to modify
and re-upload the entire firmware.
You can send capitalized 'G' as a serial command field to disable the gyro
reaction.

On Fri, Jun 23, 2023 at 11:39 PM Sam Lerman ***@***.***>
wrote:

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

--
~~
Rongzhong Li, PhD
http://borntoleave.github.io

slerman12, 2023-06-28:
I haven't tried the SkillComposer yet. It confuses me. I'm looking to do everything in Python.

Is it possible to send velocities through the serial API? It would be really helpful to see some examples of complex behaviors like flipping upright or running done with the serial API commands listed in the link you sent me.

Thanks,
Sam

borntoleave, 2023-06-29:
The skill composer can allow you to inspect the keyframes one by one and
test them on the go. The Python API can use the Skill array exported from
SkillComposer.
In serialMaster/example.py, you can see how the skill is sent to the robot.
The array "ck" is a behavior in the same format as flipping. You can start
the command with the capital 'K'.

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

--
~~
Rongzhong Li, PhD
http://borntoleave.github.io

slerman12, 2023-08-08:
Is there a simple way to read/verify that Bittle is (a) standing upright and (b) has a positive forward velocity? I retrieve 6 values from the IMU, 3 from the gyroscope and 3 from the accelerometer.

borntoleave, 2023-08-10:
Hi, you can use the token v or V to retrieve the 6-axis IMU data. Integrating the acceleration can give you speed information.

borntoleave, 2023-08-13:
The 6-axis data are defined in OpenCat/src/imu.h.
In print6Axis() prints out yaw, pitch, roll in angles, and acceleration in x, y, z directions.

The sensor can only detect acceleration rather than the current velocity. The velocity is acquired by integrating the acceleration in a specific direction. You may lose the initial speed, and the error may accumulate. Because a quadruped always wobbles and shakes during motion, you can assume that after the acceleration in all directions is stable for one second, the robot is still. Then you can use it as the integration starting point.

Closed 2022-10-25.

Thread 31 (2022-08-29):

Application crashes when using MacOS with M1

ioulosve, 2022-08-29:
I'm experiencing issues launching the Petoi Desktop App with a Macbook Pro with M1 CPU.

Launching from the Launchpad I only got this error message:

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

Launching from the terminal I got this traceback:

```
Traceback (most recent call last):
  File "/Applications/Petoi Desktop App.app/Contents/Resources/__boot__.py", line 89, in _recipes_pil_prescript
    import Image
ModuleNotFoundError: No module named 'Image'

During handling of the above exception, another exception occurred:

Traceback (most recent call last):
  File "/Applications/Petoi Desktop App.app/Contents/Resources/__boot__.py", line 135, in <module>
    _recipes_pil_prescript(['DdsImagePlugin', 'FitsStubImagePlugin', 'EpsImagePlugin', 'WmfImagePlugin', 'PdfImagePlugin', 'JpegImagePlugin', 'DcxImagePlugin', 'GbrImagePlugin', 'FpxImagePlugin', 'PalmImagePlugin', 'IptcImagePlugin', 'PsdImagePlugin', 'SunImagePlugin', 'MpegImagePlugin', 'IcoImagePlugin', 'BmpImagePlugin', 'IcnsImagePlugin', 'TgaImagePlugin', 'GifImagePlugin', 'FliImagePlugin', 'Jpeg2KImagePlugin', 'SgiImagePlugin', 'Hdf5StubImagePlugin', 'CurImagePlugin', 'PixarImagePlugin', 'BufrStubImagePlugin', 'XpmImagePlugin', 'MicImagePlugin', 'PngImagePlugin', 'BlpImagePlugin', 'WebPImagePlugin', 'PcdImagePlugin', 'FtexImagePlugin', 'MpoImagePlugin', 'MspImagePlugin', 'ImtImagePlugin', 'PpmImagePlugin', 'SpiderImagePlugin', 'PcxImagePlugin', 'GribStubImagePlugin', 'McIdasImagePlugin', 'XbmImagePlugin', 'ImImagePlugin', 'XVThumbImagePlugin', 'TiffImagePlugin'])
  File "/Applications/Petoi Desktop App.app/Contents/Resources/__boot__.py", line 93, in _recipes_pil_prescript
    from PIL import Image
  File "<frozen zipimport>", line 259, in load_module
  File "PIL/Image.pyc", line 89, in <module>
  File "<frozen zipimport>", line 259, in load_module
  File "PIL/_imaging.pyc", line 14, in <module>
  File "PIL/_imaging.pyc", line 10, in __load
  File "imp.pyc", line 342, in load_dynamic
ImportError: dlopen(/Applications/Petoi Desktop App.app/Contents/Resources/lib/python3.9/lib-dynload/PIL/_imaging.so, 0x0002): Library not loaded: '@rpath/libtiff.5.dylib'
  Referenced from: '/Applications/Petoi Desktop App.app/Contents/Resources/lib/python3.9/lib-dynload/PIL/_imaging.so'
  Reason: tried: '/opt/anaconda3/envs/simpleUI/lib/libtiff.5.dylib' (no such file), '/opt/anaconda3/envs/simpleUI/lib/libtiff.5.dylib' (no such file), '/Applications/Petoi Desktop App.app/Contents/Resources/lib/python3.9/lib-dynload/PIL/../../../libtiff.5.dylib' (no such file), '/opt/anaconda3/envs/simpleUI/lib/libtiff.5.dylib' (no such file), '/opt/anaconda3/envs/simpleUI/lib/libtiff.5.dylib' (no such file), '/Applications/Petoi Desktop App.app/Contents/Resources/lib/python3.9/lib-dynload/PIL/../../../libtiff.5.dylib' (no such file), '/opt/anaconda3/envs/simpleUI/lib/libtiff.5.dylib' (no such file), '/Applications/Petoi Desktop App.app/Contents/Frameworks/libtiff.5.dylib' (no such file), '/Applications/Petoi Desktop App.app/Contents/MacOS/../Frameworks/libtiff.5.dylib' (no such file), '/usr/local/lib/libtiff.5.dylib' (no such file), '/usr/lib/libtiff.5.dylib' (no such file)
2022-08-29 10:16:05.365 Petoi Desktop App[7205:38695] Launch error
2022-08-29 10:16:05.365 Petoi Desktop App[7205:38695] Launch error
See the py2app website for debugging launch issues
exit
```

I also tried directly from source code cloning this repo and starting pyUI/UI.py after have installed pyserial and pillow packages and the application starts showing the small window with the three buttons but then, when I choose Skill Composer it crashes with a Segmentation fault error when I click on the Behavior or Export buttons.

Is there something I'm missing?

Thanks in advance for the help

borntoleave, 2022-08-30:
I developed the code on an M1 mac, so there shouldn't be a compatibility
issue.
Since you have tried to install pillow, but the program still reports a "No
module named 'Image'" error, I suggest you check if your python library
path and the running path are the same.

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

--
~~
Rongzhong Li, PhD
http://borntoleave.github.io

ioulosve, 2022-08-31:
Checking the traceback I noticed that the App searches for `/opt/anaconda3/envs/simpleUI/lib/libtiff.5.dylib` library so I installed anaconda (I was using minicoda before) and then I created a enviroment called simpleUI where I installed pillow and pyserial.

Now the Petoi Desktop App found that library but it says that the architecture is incompatible (have arm64, need x86_64).

What I'm supposed to do now?

```
Traceback (most recent call last):
  File "/Applications/Petoi Desktop App.app/Contents/Resources/__boot__.py", line 89, in _recipes_pil_prescript
    import Image
ModuleNotFoundError: No module named 'Image'

During handling of the above exception, another exception occurred:

Traceback (most recent call last):
  File "/Applications/Petoi Desktop App.app/Contents/Resources/__boot__.py", line 135, in <module>
    _recipes_pil_prescript(['DdsImagePlugin', 'FitsStubImagePlugin', 'EpsImagePlugin', 'WmfImagePlugin', 'PdfImagePlugin', 'JpegImagePlugin', 'DcxImagePlugin', 'GbrImagePlugin', 'FpxImagePlugin', 'PalmImagePlugin', 'IptcImagePlugin', 'PsdImagePlugin', 'SunImagePlugin', 'MpegImagePlugin', 'IcoImagePlugin', 'BmpImagePlugin', 'IcnsImagePlugin', 'TgaImagePlugin', 'GifImagePlugin', 'FliImagePlugin', 'Jpeg2KImagePlugin', 'SgiImagePlugin', 'Hdf5StubImagePlugin', 'CurImagePlugin', 'PixarImagePlugin', 'BufrStubImagePlugin', 'XpmImagePlugin', 'MicImagePlugin', 'PngImagePlugin', 'BlpImagePlugin', 'WebPImagePlugin', 'PcdImagePlugin', 'FtexImagePlugin', 'MpoImagePlugin', 'MspImagePlugin', 'ImtImagePlugin', 'PpmImagePlugin', 'SpiderImagePlugin', 'PcxImagePlugin', 'GribStubImagePlugin', 'McIdasImagePlugin', 'XbmImagePlugin', 'ImImagePlugin', 'XVThumbImagePlugin', 'TiffImagePlugin'])
  File "/Applications/Petoi Desktop App.app/Contents/Resources/__boot__.py", line 93, in _recipes_pil_prescript
    from PIL import Image
  File "<frozen zipimport>", line 259, in load_module
  File "PIL/Image.pyc", line 89, in <module>
  File "<frozen zipimport>", line 259, in load_module
  File "PIL/_imaging.pyc", line 14, in <module>
  File "PIL/_imaging.pyc", line 10, in __load
  File "imp.pyc", line 342, in load_dynamic
ImportError: dlopen(/Applications/Petoi Desktop App.app/Contents/Resources/lib/python3.9/lib-dynload/PIL/_imaging.so, 0x0002): Library not loaded: '@rpath/libtiff.5.dylib'
  Referenced from: '/Applications/Petoi Desktop App.app/Contents/Resources/lib/python3.9/lib-dynload/PIL/_imaging.so'
  Reason: tried: '/opt/anaconda3/envs/simpleUI/lib/libtiff.5.dylib' (mach-o file, but is an incompatible architecture (have (arm64), need (x86_64))), '/opt/anaconda3/envs/simpleUI/lib/libtiff.5.dylib' (mach-o file, but is an incompatible architecture (have (arm64), need (x86_64))), '/Applications/Petoi Desktop App.app/Contents/Resources/lib/python3.9/lib-dynload/PIL/../../../libtiff.5.dylib' (no such file), '/opt/anaconda3/envs/simpleUI/lib/libtiff.5.dylib' (mach-o file, but is an incompatible architecture (have (arm64), need (x86_64))), '/opt/anaconda3/envs/simpleUI/lib/libtiff.5.dylib' (mach-o file, but is an incompatible architecture (have (arm64), need (x86_64))), '/Applications/Petoi Desktop App.app/Contents/Resources/lib/python3.9/lib-dynload/PIL/../../../libtiff.5.dylib' (no such file), '/opt/anaconda3/envs/simpleUI/lib/libtiff.5.dylib' (mach-o file, but is an incompatible architecture (have (arm64), need (x86_64))), '/Applications/Petoi Desktop App.app/Contents/Frameworks/libtiff.5.dylib' (no such file), '/Applications/Petoi Desktop App.app/Contents/MacOS/../Frameworks/libtiff.5.dylib' (no such file), '/usr/local/lib/libtiff.5.dylib' (no such file), '/usr/lib/libtiff.5.dylib' (no such file)
2022-08-31 17:25:43.758 Petoi Desktop App[11550:81866] Launch error
2022-08-31 17:25:43.758 Petoi Desktop App[11550:81866] Launch error
See the py2app website for debugging launch issues
```

ioulosve, 2022-09-02:
Ok I solved it installing the x86_64 version of anaconda3 in /opt/anaconda3, creating the simpleUI environment and installing the pyserial and pillow packages inside it.

I hope these information can help someone with the same problem

Thank you for the support

Closed 2022-09-02.

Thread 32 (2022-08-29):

Is this a bug? I can't understand the logic here

yaringal, 2022-08-29:
https://github.com/PetoiCamp/OpenCat/blob/1abeb1cf15f4dda2b9f16e23810eb3a9e0289fd1/src/motion.h#L65

borntoleave, 2022-08-30:
for (i % 4 < 2) ? ( RollPitchDeviation[1]) : RollPitchDeviation[1]

It's not a bug but a useless branch condition. Previously I tested two
cases but then deleted the factors in the first case. That's why the first
RollPitchDeviation[1] has parentheses around it. I left it there in case I
want to experiment more in the future.

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

--
~~
Rongzhong Li, PhD
http://borntoleave.github.io

borntoleave, 2022-08-30:
The expected body orientation is a reference angle used to tell how much
the robot is off the right position. The error is fed into a simple
feedback calculation. My code only tries to reduce the error, but not to
eliminate it. Ideally, if you design a good PID control, you may attain the
specified expected body orientation.

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

--
~~
Rongzhong Li, PhD
http://borntoleave.github.io

Closed 2022-10-25.

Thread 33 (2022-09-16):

Example code for Task creation

sam-tj, 2022-09-16:
Is there a sample code which integrates the Digital / Analog pins with the base code (OpenCat.ino)

For example,
The robot should be moving forward but should stop when ultrasonic detects an object within certain range. This must be done using Arduino IDE (C++) but as per the source codes, I couldn't find an example for such integration of io pins with per-defined skills.

borntoleave, 2022-10-25:
I just updated OpenCat.ino to include a simple demo that triggers skills with an input pin.

Closed 2022-11-01.

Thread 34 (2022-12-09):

Running the Firmware Uploader on a Raspberry PI does not work

elgohary12, 2022-12-09:
I tried to run the firmware uploader from the UI on a raspberry pi, but it isn't able to connect to the correct port (/dev/ttyS0). The calibrator however works on the raspberry pi.  After looking at the code we found that the communication is established differently in the calibrator and in the firmware uploader. In the calibrator, ardSerial is used while in the firmware uploader serial.tools.list_ports is used. Is there a way in which we can use the ardSerial in the firmware uploader? Thanks for the help.

borntoleave, 2022-12-11:
When you mount the Pi on the NyBoard, they communicate through the serial port. However, when you want to upload firmware, it will also use the reset signal. With the USB uploader connected to the 6-pin socket, the reset signal is automatically sent through the DTR pin. While with the 2x5 socket, we haven't integrated it directly into the firmware uploader. There's a [forum post ](https://www.petoi.camp/forum/hardware/how-to-setup-raspberry-pi-for-programming-nybble-without-ftdi-module)discussing the differences between the two interfaces.

Closed 2025-03-01.

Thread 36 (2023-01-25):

Changing the speed of "Walk"

Jakob0330, 2023-01-25:
I'm currently working on a project with Bittle. I want to change the speed of walking but haven't found parameters for speed of this action in the skillfile. Does anyone solve this problem before？

borntoleave, 2023-01-25:
You can change the walking speed in many ways:
- Use faster gaits such as trot.
- Add delays between frames to slow the speed down.
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

- Re-generate the walking gait with different numbers of frames. The fewer frames, the faster; the more frames, the slower and smoother. However, due to the limited memory size of NyBoard, the frames should be less than (450-4)/8 = 55, as the array to store the gait is defined by `int8_t *dataBuffer = new int8_t[450];` in src/OpenCat.h
- Buy the [ESP32-based BiBoard](https://www.petoi.com/products/petoi-biboard-esp32-development-board) with a faster CPU and a larger memory. The code can be found in [https://github.com/PetoiCamp/OpenCatEsp32](https://github.com/PetoiCamp/OpenCatEsp32)

Closed 2023-06-08.

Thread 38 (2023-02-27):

MU Camera using arduino IDE error

Getafix17, 2023-02-27:
I just got a  camera module, when I uncomment  // [#define](https://www.youtube.com/hashtag/define) CAMERA   //for BallTracking using Mu Vision camera I get the following error in Arduino IDE
Arduino: 1.8.19 (Windows 10), Board: "Arduino Uno"
In file included from C:\Users\alexf\Desktop\Petoi Bittle\Bittle OpenCat\OpenCat\src\OpenCat.h:443:0,

                 from C:\Users\alexf\Desktop\Petoi Bittle\Bittle OpenCat\OpenCat\OpenCat.ino:81:

C:\Users\alexf\Desktop\Petoi Bittle\Bittle OpenCat\OpenCat\src\reaction.h: In function 'void reaction()':

C:\Users\alexf\Desktop\Petoi Bittle\Bittle OpenCat\OpenCat\src\reaction.h:340:24: error: expected primary-expression before ':' token

       case T_TASK_QUEUE:

                        ^

exit status 1

Error compiling for board Arduino Uno.
I tried using the bug fix recommended by Petoi camp In src/opencat.h, find #define T_TASK_QUEUE, add space and ‘q’ after it.
#define T_TASK_QUEUE ‘q’ did not work either.

borntoleave, 2023-02-27:
Try using [this version](https://github.com/PetoiCamp/OpenCat/tree/beforeInplace) in the working branch. It will be merged into the main after a thorough test.

Getafix17, 2023-02-27:
Thanks that worked, I was able to compile the code without error after uncommenting #define CAMERA //

Closed 2023-02-27.

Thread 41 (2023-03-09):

very-long-line-length-in-source-file  > 512

atzlinux, 2023-03-09:
When I make deb package for this repo, Debian check tool find the some files's line is very long.

I suggest to modify them:

very-long-line-length-in-source-file 9290 > 512 [ModuleTests/ESP8266WiFiController/mainpage.h:7]
very-long-line-length-in-source-file 782 > 512 [README.md:13]
very-long-line-length-in-source-file 602 > 512 [ModuleTests/ESP8266WiFiController/calibrationpage.h:9]

Thanks!

atzlinux, 2023-03-10:
This is the Debian's explanation about this check:

N:
P: very-long-line-length-in-source-file
N:
N:   The source file includes a line length that is well beyond the normally
N:   human made code line length.
N:
N:   This very long line length does not allow Lintian to do correctly some
N:   source file checks.
N:
N:   This line could also be the result of some text injected by a computer
N:   program, and thus could lead to FTBFS bugs.
N:
N:   Last but not least, long line in source code could be used to obfuscate
N:   the source code and to hide stuff like backdoors or security problems.
N:
N:   It could be due to jslint source comments or other build tool comments.
N:
N:   You may report this issue upstream.

Certainly, this is only a suggestion for deb packaging.

The README.md  file is included in the desktop app deb package as a user
document.

在 2023/3/9 17:18, Rongzhong Li 写道:
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

--
肖盛文 xiao sheng wen
微信(wechat)：atzlinux
《铜豌豆 Linux》https://www.atzlinux.com
基于 Debian 的 Linux 中文 桌面 操作系统
GnuPG Public Key: 0x2F338C7DC7909957

borntoleave, 2023-03-10:
The extremely long string in mainpage.h is the base64 format of our logo
image.
The Readme has been updated to shorter sentences.
The calibration page has a long paragraph section. It could be split.

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

--
~~
Rongzhong Li, PhD
http://borntoleave.github.io

Closed 2023-03-16.

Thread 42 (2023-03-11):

Unable to upload code after bluetooth connection failed

Getafix17, 2023-03-11:
After I tried to upload the new main sketch it failed to connect to bluetooth. Now for some reason I cannot  upload anything with the Arduino IDE or desktop apk.

Error from Arduino IDE

Arduino: 1.8.19 (Windows 10), Board: "Arduino Uno"

Sketch uses 24486 bytes (75%) of program storage space. Maximum is 32256 bytes.

Global variables use 1471 bytes (71%) of dynamic memory, leaving 577 bytes for local variables. Maximum is 2048 bytes.

An error occurred while uploading the sketch

avrdude: stk500_recv(): programmer is not responding

avrdude: stk500_getsync() attempt 1 of 10: not in sync: resp=0x7d

avrdude: stk500_recv(): programmer is not responding

avrdude: stk500_getsync() attempt 2 of 10: not in sync: resp=0x7d

avrdude: stk500_recv(): programmer is not responding

avrdude: stk500_getsync() attempt 3 of 10: not in sync: resp=0x7d

avrdude: stk500_recv(): programmer is not responding

avrdude: stk500_getsync() attempt 4 of 10: not in sync: resp=0x7d

avrdude: stk500_recv(): programmer is not responding

avrdude: stk500_getsync() attempt 5 of 10: not in sync: resp=0x7d

avrdude: stk500_recv(): programmer is not responding

avrdude: stk500_getsync() attempt 6 of 10: not in sync: resp=0x7d

avrdude: stk500_recv(): programmer is not responding

avrdude: stk500_getsync() attempt 7 of 10: not in sync: resp=0x7d

avrdude: stk500_recv(): programmer is not responding

avrdude: stk500_getsync() attempt 8 of 10: not in sync: resp=0x7d

avrdude: stk500_recv(): programmer is not responding

avrdude: stk500_getsync() attempt 9 of 10: not in sync: resp=0x7d

avrdude: stk500_recv(): programmer is not responding

avrdude: stk500_getsync() attempt 10 of 10: not in sync: resp=0x7d

This report would have more information with
"Show verbose output during compilation"
option enabled in File -> Preferences.

borntoleave, 2023-03-11:
Try to upload the sketch using the USB uploader. It's more stable than the
Bluetooth dongle.
When using the USB uploader, observe its LEDs. Is the yellow LED constantly
lighting up or does it blink after you press the upload button?

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

--
~~
Rongzhong Li, PhD
http://borntoleave.github.io

Getafix17, 2023-03-11:
I am using the USB uploader. The yellow LED is constant not blinking, Also the beeping sounds I used to get while connecting the robot have stopped and the robot is completly dead.

Getafix17, 2023-03-11:
Desktop apk also gives an upload error

borntoleave, 2023-03-11:
The Arduino bootloader may be crashed. Please check this section to reset:
[Burn the bootloader](https://docs.petoi.com/arduino-ide/upload-sketch-for-nyboard#burn-the-bootloader-no-need-for-normal-use)

Getafix17, 2023-03-11:
Thanks Dr. Li. I will try to reset the bootloader. I will close for now.
P.S. I am a big fan of your work!

Getafix17, 2023-03-11:
I have an Arduino UNO. According to the documentation, "The programming process uses VCC, GND and four data pins. Three pins connect MISO (pin12), MOSI(Pin11) and SCK(pin13) between the programming micro and the target micro, the fourth pin from the programming micro goes to the reset pin of the target."
The serial USB adapter has GND,RTS, RX, TX, 5V,GND, DTR. How do I connect these to the corresponding arduino pins using jumper wires. Also how could I know if it is a hardware problem?

borntoleave, 2023-03-12:
I just added a pinout picture in the user manual. Please check.
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

Getafix17, 2023-03-12:
Thank you sir, I have one more question, please forgive my ignorance. Can I connect the jumper wires directly from the top of the board. I used jumper wires and the contact seems loose.

borntoleave, 2023-03-12:
You can press the pins slightly to ensure the connections. It's a onetime operation, so no need for soldering.

Getafix17, 2023-03-12:
Thanks for your patience sir. I will try it out.

Closed 2023-03-12.

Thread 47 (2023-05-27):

Adding to siri, but not work in siri.

gscfwid, 2023-05-27:
It seemed that when I firts time added opencat to siri it worked well. But recently, it prompts that "chat长时间未响应”, meaning "chat not respond for a long time".

borntoleave, 2023-05-27:
Hi, Could you specify how you are connecting OpenCat to Siri?

On Sat, May 27, 2023 at 11:16 AM Shaowei Gao ***@***.***>
wrote:

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

--
~~
Rongzhong Li, PhD
http://borntoleave.github.io

borntoleave, 2023-11-08:
It appears to be another OpenCat app.

Closed 2023-11-08.

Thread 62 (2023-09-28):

opencat app bug : Team: 网络连接已中断。

xiguaABei, 2023-09-28:
today ，i use opencat app , when i send message i shows a toast Team: 网络连接已中断。

JasonWong08, 2023-09-29:
> today ，i use opencat app , when i send message i shows a toast Team: 网络连接已中断。

what's the app? Petoi Desktop App or smartphone app?

borntoleave, 2023-11-08:
> today ，i use opencat app , when i send message i shows a toast Team: 网络连接已中断。

It appears to be another app that's using our OpenCat name.

Closed 2023-11-08.

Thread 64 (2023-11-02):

After uploading the code of OpenCat.ino Robot will not accept any new code.

JEAPI-DEV, 2023-11-02:
So I wanted to upload the OpenCat.ino Program for testing, and it worked but after doing so it's Buzzer piped and after that I was not able to upload any new code to the Bittle Bot. Be it over https://ide.tinkergen.com/ or via the Arduino IDE.

So then I tried uploading the factory code explained in the documentation. But this is the error I got:

`C:\Users\jeapi\AppData\Local\Programs\cc-assistant\resources\script\arduino\opencat>"C:\Users\jeapi\AppData\Local\Programs\cc-assistant\resources\compilers\arduino"\contents\hardware\tools\avr\bin\avrdude -C"C:\Users\jeapi\AppData\Local\Programs\cc-assistant\resources\compilers\arduino"\contents\hardware\tools\avr\etc\avrdude.conf -v -patmega328p -carduino -P"COM10" -b115200 -D -Uflash:w:"C:\Users\jeapi\AppData\Local\Programs\cc-assistant\resources\buildTemp\arduino\opencat\grove_.ino.hex":i C:\Users\jeapi\AppData\Local\Programs\cc-assistant\resources\script\arduino\opencat>del "C:\Users\jeapi\AppData\Local\Programs\cc-assistant\resources\buildTemp\arduino\opencat\grove_.ino.hex" avrdude: Version 6.3, compiled on Jan 17 2017 at 12:00:53 Copyright (c) 2000-2005 Brian Dean, http://www.bdmicro.com/ Copyright (c) 2007-2014 Joerg Wunsch System wide configuration file is "C:\Users\jeapi\AppData\Local\Programs\cc-assistant\resources\compilers\arduino\contents\hardware\tools\avr\etc\avrdude.conf" Using Port : COM10 Using Programmer : arduino Overriding Baud Rate : 115200 avrdude: stk500_recv(): programmer is not responding avrdude: stk500_getsync() attempt 1 of 10: not in sync: resp=0xbd avrdude: stk500_recv(): programmer is not responding avrdude: stk500_getsync() attempt 2 of 10: not in sync: resp=0xbd avrdude: stk500_recv(): programmer is not responding avrdude: stk500_getsync() attempt 3 of 10: not in sync: resp=0xbd avrdude: stk500_recv(): programmer is not responding avrdude: stk500_getsync() attempt 4 of 10: not in sync: resp=0xbd avrdude: stk500_recv(): programmer is not responding avrdude: stk500_getsync() attempt 5 of 10: not in sync: resp=0xbd avrdude: stk500_recv(): programmer is not responding avrdude: stk500_getsync() attempt 6 of 10: not in sync: resp=0xbd avrdude: stk500_recv(): programmer is not responding avrdude: stk500_getsync() attempt 7 of 10: not in sync: resp=0xbd avrdude: stk500_recv(): programmer is not responding avrdude: stk500_getsync() attempt 8 of 10: not in sync: resp=0xbd avrdude: stk500_recv(): programmer is not responding avrdude: stk500_getsync() attempt 9 of 10: not in sync: resp=0xbd avrdude: stk500_recv(): programmer is not responding avrdude: stk500_getsync() attempt 10 of 10: not in sync: resp=0xbd avrdude done. Thank you.
`

Thanks in advance.

JEAPI-DEV, 2023-11-02:
The problem seems to be So the problem seems to be that I flashed this code, but forgot to chnage the NyBoard to NvBoard_V1_1. It was set by default to NyBoard_V1_2 .

borntoleave, 2023-11-02:
The board version definition shouldn't block new uploads.
Please follow this debugging routine:
https://docs.petoi.com/technical-support/faq-frequently-asked-questions#nyboard-cant-upload-firmware

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

--
~~
Rongzhong Li, PhD
http://borntoleave.github.io

Closed 2023-11-02.

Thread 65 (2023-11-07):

Sketch too big for NyBoard V0_2

wack-back, 2023-11-07:
When compile with #define MAIN_SKETCH uncomment, the arduino gives:
Sketch uses 31824 bytes (103%) of program storage space. Maximum is 30720 bytes.
Global variables use 1596 bytes (77%) of dynamic memory, leaving 452 bytes for local variables. Maximum is 2048 bytes.
Sketch too big; see https://support.arduino.cc/hc/en-us/articles/360013825179 for tips on reducing it.
text section exceeds available space in board

Any way can solve this?

borntoleave, 2023-11-08:
NyBoard V0_* used a 20MHz crystal faster than standard Uno's 16MHz. Its bootloader is borrowed from Arduino Pro mini and takes more space. We've added new functions to the original code until it filled up NyBoard V1_* and exceeded NyBoardV0_*.

The mobile app has already replaced the infrared remote's functionality. You may turn off the infrared remote module by commenting out this line at the beginning of OpenCat.h. The size will be reduced to 99%.
`// #define IR_PIN 4  // Signal Pin of IR receiver to Arduino Digital Pin 4`
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

Alternatively, you may try our new boards:

- [Uno-equivalent NyBoard V1](https://www.petoi.com/products/nyboard-customized-arduino-board)

- [ESP32-based BiBoard](https://www.petoi.com/products/biboard-esp32-development-board-for-quadruped-robot)

wack-back, 2023-11-16:
Thank you for solving this issue!

Closed 2023-11-16.

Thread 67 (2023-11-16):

Petoi Bluetooth Adapter not compatible with NyBoard_V02 ?

wack-back, 2023-11-16:
I bought Petoi Bluetooth Adapter, and plug it into the NyBoard_V02.
However, the mobile app seems not compatible with it.
I tried both Apps in https://docs.petoi.com/mobile-app/introduction
I can see the PetoiBLE-9ACC listed in Petoi app. But when I click on link button, the NyBoard restarts, and App shows can't find Petoi device.
Anyway I can solve this? or I can only use Petoi Bluetooth Adapter as a remote uart?

wack-back, 2023-11-17:
Issue solved! It's because the NyBoard_V02 baudrate default to 57600, but BLE is 115200 as default.
Just change the baudrate in OpenCat.h
Problem Solved!

borntoleave, 2023-11-17:
> Issue solved! The NyBoard_V02 baudrate defaults to 57600, but BLE is 115200 as default. Just change the baudrate in OpenCat.h Problem Solved!

Ah, yes, It's been quite a while, and I just forgot to mention the difference in Baudrate. Glad that you pointed it out.

Closed 2023-11-17.

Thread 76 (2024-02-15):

Is there a way to disable the beep sound?

Kakcalu13, 2024-02-15:
It beeps so much that it disturbed my team lol

borntoleave, 2024-02-17:
Yes, you can send a single 'b' to the serial port mute/unmute the beeps.
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

You can even delete the lines with beep() function.
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

Closed 2024-02-17.

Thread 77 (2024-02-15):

Getting data from IMU data (such as YRP and Accelerators) on the main source

Kakcalu13, 2024-02-15:
https://github.com/PetoiCamp/OpenCat/blob/main/OpenCat.ino

I'm using above as a main source. I don't see any IMU data. I tried to do the same thing from this file, https://github.com/PetoiCamp/OpenCat/tree/main/ModuleTests/testMPU on the main source and it end up insufficient memory to upload.

What do you suggest? No matter what I do, I break everything when I tried something in the main source

Kakcalu13, 2024-02-17:
i was able to print after ran a command 'V' but it only displays 2 things instead of 3. I also wanted to display acceleration + gyro in real time

borntoleave, 2024-02-19:
In src/imu.h, in print6Axis(), you can enable the line for the yaw
(ypr[0]). YPR means yaw pitch roll, corresponding to 0,1,2.
If the flash runs low, you can comment out the *#define IR_PIN* line to
save some space.

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

--
~~
Rongzhong Li, PhD
http://borntoleave.github.io

Kakcalu13, 2024-02-19:
those worked!! thank you so much! What about the acceleration?

borntoleave, 2024-02-20:
You can refer to OpenCat/ModuleTests/testMPU/testMPU.ino and activate the
defined macros to print the accelerations. Then add those statements to the
OpenCat code.

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

--
~~
Rongzhong Li, PhD
http://borntoleave.github.io

Kakcalu13, 2024-02-20:
Hi there,

I truly appreciate your time!

I tried that and the memory end up maxed. See here:

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

All I did was update this in the imu.h

```
// #define READ_ACCELERATION
void print6Axis() {
  PT_FMT(ypr[0], 5);
  PT('\t');
  PT_FMT(ypr[1], 5);
  PT('\t');
  PT_FMT(ypr[2], 5);
  PT("\t");
  mpu.dmpGetQuaternion(&q, fifoBuffer);
  mpu.dmpGetAccel(&aa, fifoBuffer);
  mpu.dmpGetGravity(&gravity, &q);
  mpu.dmpGetLinearAccel(&aaReal, &aa, &gravity);
  mpu.dmpGetLinearAccelInWorld(&aaWorld, &aaReal, &q);
  Serial.print("aworld\t");
  Serial.print(aaWorld.x);
  Serial.print("\t");
  Serial.print(aaWorld.y);
  Serial.print("\t");
  Serial.println(aaWorld.z);
```

I even tried to do it on OpenCat.h:

```
#ifdef GYRO_PIN
  for (byte r = 0; r < 50; r++) {  //ypr is slow when starting up. leave enough time between IMU initialization and this reading
    read_IMU();
    mpu.dmpGetQuaternion(&q, fifoBuffer);
    mpu.dmpGetAccel(&aa, fifoBuffer);
    mpu.dmpGetGravity(&gravity, &q);
    mpu.dmpGetLinearAccel(&aaReal, &aa, &gravity);
    mpu.dmpGetLinearAccelInWorld(&aaWorld, &aaReal, &q);
    Serial.print("aworld\t");
    Serial.print(aaWorld.x);
    Serial.print("\t");
    Serial.print(aaWorld.y);
    Serial.print("\t");
    Serial.println(aaWorld.z);
    delay(10);
  }
  token = (fabs(ypr[1]) > 30 || fabs(ypr[2]) > 30) ? T_CALIBRATE : T_REST;  //put the robot's side on the table to enter calibration posture for attaching legs
  newCmdIdx = 2;
  int rndSeed = ypr[2] * 10000;
#else
  int rndSeed = analogRead(A2);
#endif
```

I must be doing something wrong. Can you tell me which is the macros? Also do you happen to have a doc to show where or how?

borntoleave, 2024-02-21:
By disabling this IR_PIN, you can save 4% of the flash.
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

Kakcalu13, 2024-02-21:
Thank you for your time again!

Yeah, it's already disabled.
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

I was just confused about how this code snippet ended up consuming more memory than IR when it's just 11 lines:

```cpp
  mpu.dmpGetQuaternion(&q, fifoBuffer);
  mpu.dmpGetAccel(&aa, fifoBuffer);
  mpu.dmpGetGravity(&gravity, &q);
  mpu.dmpGetLinearAccel(&aaReal, &aa, &gravity);
  mpu.dmpGetLinearAccelInWorld(&aaWorld, &aaReal, &q);
  Serial.print("aworld\t");
  Serial.print(aaWorld.x);
  Serial.print("\t");
  Serial.print(aaWorld.y);
  Serial.print("\t");
  Serial.println(aaWorld.z);
```

See here in `opencat.h`:

```cpp
#ifdef GYRO_PIN
  for (byte r = 0; r < 50; r++) {  //ypr is slow when starting up. leave enough time between IMU initialization and this reading
    read_IMU();

// Add new section from testIMU code.
    mpu.dmpGetQuaternion(&q, fifoBuffer);
    mpu.dmpGetAccel(&aa, fifoBuffer);
    mpu.dmpGetGravity(&gravity, &q);
    mpu.dmpGetLinearAccel(&aaReal, &aa, &gravity);
    mpu.dmpGetLinearAccelInWorld(&aaWorld, &aaReal, &q);
    Serial.print("aworld\t");
    Serial.print(aaWorld.x);
    Serial.print("\t");
    Serial.print(aaWorld.y);
    Serial.print("\t");
    Serial.println(aaWorld.z);
// End of the new code inserted above

    delay(10);
  }
  token = (fabs(ypr[1]) > 30 || fabs(ypr[2]) > 30) ? T_CALIBRATE : T_REST;  //put the robot's side on the table to enter calibration posture for attaching legs
  newCmdIdx = 2;
  int rndSeed = ypr[2] * 10000;
#else
  int rndSeed = analogRead(A2);
#endif
```

So, based on your response, it sounds like I did the right thing with the macro part. I saw that it saved 4% of flash!

borntoleave, 2024-02-22:
The MPU calls a heavy library that uses many parameters and algorithms to calculate.

Kakcalu13, 2024-03-04:
Thanks! Truly appreciate your time!

Closing this issue since we have forum now and it's more active and most people go there so I'm going to be there so people can search for the similar question over there

Closed 2024-03-04.

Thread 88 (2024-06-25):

ardSerial.py suggestion

gravesreid, 2024-06-25:
From lines 673 to 699 in ardserial.py:

def showSerialPorts(allPorts):
    # currently an issue in pyserial where for newer raspiberry pi os
    # (Kernel version: 6.1, Debian version: 12 (bookworm)) or ubuntus (22.04)
    # it classifies the /dev/ttyS0 port as a platform port and therefore won't be queried
    # https://github.com/pyserial/pyserial/issues/489
    if os.name == 'posix' and sys.platform.lower()[:5] == 'linux':
        extra_ports = glob.glob('/dev/ttyS*')
        for port in extra_ports:
            if port not in allPorts:
                allPorts.append(port)
        for item in allPorts:
            if 'AMA0' in item:
                allPorts.remove(item)

    allPorts = deleteDuplicatedUsbSerial(allPorts)
    for index in range(len(allPorts)):
        logger.debug(f"port[{index}] is {allPorts[index]} ")
    print("\n*** Available serial ports: ***")
    print(*allPorts, sep = "\n")
    if platform.system() != "Windows":
        for p in allPorts:
             if 'cu.usb' in p:
                print('\n* Manually connect to the following port if it fail to connect automatically\n')
                if config.useMindPlus:
                    print(p.replace('/dev/',''),end='\n\n')
                else:
                    print(p, end='\n\n')
            
I suggest removing:
        for item in allPorts:
            if 'AMA0' in item:
                allPorts.remove(item)
        
I had to remove this to get ardserial to work, as port /dev/ttyS0 doesn't work for me, however, ttyAMA0 is available, but this line loop removes the possibility of connecting to it

borntoleave, 2024-06-28:
We removed the AMA0 because querying AMA0 will lead to a dead thread when
sending handshaking signals.
The new BiBoard will have an independent serial port to communicate with
Pi, so ttyS0 should always work. I'd keep the current code.

On Wed, Jun 26, 2024 at 1:40 AM Reid Graves ***@***.***>
wrote:

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

--
~~
Rongzhong Li, PhD
http://borntoleave.github.io

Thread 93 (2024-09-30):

Use gyro and ultrasonic eyes

josephburnett, 2024-09-30:
Currently the software cannot use the gyro and ultrasonic eyes at the same time.

https://github.com/PetoiCamp/OpenCat/blob/902c3192224833202c429f59df9678b60d838989/OpenCat.ino#L55

Is this a software limitation (making the compiled code smaller) or a hardware limitation (not enough registers)? I am interested in improving the code to have both working at the same time.

borntoleave, 2024-10-01:
ATmega328P only has 32 KB flash and 2 KB SRAM. The added features and UI eventually filled up the programming space (Flash), making it difficult to run two large modules simultaneously. The 64Kb I2C EEPROM used for saving behaviors data is also filled up. You can comment out the IR_PIN and disable the Neopixels in the Ultrasonic sensor to save space for the Gyro.

We are moving to [OpenCatESP32](https://github.com/PetoiCamp/OpenCatEsp32), where the computational resources are more abundant.

borntoleave, 2025-03-01:
The newer version that runs on ESP32 allows the use of gyro and ultrasonic eyes simultaneously.
https://github.com/PetoiCamp/OpenCatEsp32/

Closed 2025-03-01.

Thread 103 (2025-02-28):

NameError: name 'languageList' is not defined

DarwinJS, 2025-02-28:
Current version of master as of the time this issue was created

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

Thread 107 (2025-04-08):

Ability to read IMU data with v1.2.4

abpolym, 2025-04-08:
Hey! I just saw that you released [a new version](https://github.com/PetoiCamp/OpenCat/releases/tag/1.2.4) which contained the following statement for the firmware:

* Allow reading IMU data via the serial protocol

I would like to read all IMU data (accelerometer and gyroscope data in all three directions).
How can I do that?

From what I understood, there are two functions defined in [imu.h](https://github.com/PetoiCamp/OpenCat/blob/main/src/imu.h) that are called in [reaction.h](https://github.com/PetoiCamp/OpenCat/blob/main/src/reaction.h):

* [print6Axis](https://github.com/PetoiCamp/OpenCat/blob/main/src/imu.h#L168-L188) is [triggered](https://github.com/PetoiCamp/OpenCat/blob/main/src/reaction.h#L136) when sending a [v or V token](https://github.com/PetoiCamp/OpenCat/blob/main/src/OpenCat.h#L235-L236). Since `READ_ACCELERATION` is not defined per default and printing the first index of `ypr` (yaw pitch roll) is commented out, this would return only 2 out of 6 possible values: pitch and roll.
* [read_IMU](https://github.com/PetoiCamp/OpenCat/blob/main/src/imu.h#L189-L230) is triggered in multiple instances; 1) whenever readEnvironment (such as in the [driver's loop function](https://github.com/PetoiCamp/OpenCat/blob/main/OpenCat.ino#L104)), 2) [when the robot is initialized](https://github.com/PetoiCamp/OpenCat/blob/main/src/OpenCat.h#L516C8-L526), and 3) in [the perform function of src/skill.h](https://github.com/PetoiCamp/OpenCat/blob/main/src/skill.h#L409-L430) which is triggered whenever a skill (triggered by the [`k` and possibly `K` tokens in OpenCat.h](https://github.com/PetoiCamp/OpenCat/blob/main/src/OpenCat.h#L226-L227)) is being performed? All instances require `GYRO_PIN` to be defined, which is the case by default. However, I do not immediately see how to then retrieve all 6 gyro/acc values.

Is there a way to retrieve acceleration/orientation in all three directions by default or do I have to modify, recompile, and upload the modified firmware?

borntoleave, 2025-04-10:
Hi,
We have modified the print gyro token to gP, at the bottom of the table:
https://docs.petoi.com/apis/serial-protocol

You can modify the printGyroQ = true to print the values by default.
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

borntoleave, 2025-04-10:
It will print 6-axis data. Oh, BTW, only the ESP32-based board will print
all 6 data. The NyBoard version must modify the code because the default
firmware has used up all the flash for the generic UI.

On Thu, Apr 10, 2025 at 7:53 PM polym (Tim) ***@***.***>
wrote:

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

--
~~
Rongzhong Li, PhD
http://borntoleave.github.io

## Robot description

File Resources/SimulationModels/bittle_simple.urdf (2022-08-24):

<?xml version="0.0" ?>
<robot name="bittle_simple">
	<link name="torso">
		<inertial>
			<origin rpy="0.00000 -0.00000 0.00000" xyz="0.00000 0.00000 0.00000"/>
			<mass value="20.00000"/>
			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
		</inertial>
		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
	</link>
	<link name="link1_2">
		<inertial>
			<origin rpy="0.00000 -0.00000 0.00000" xyz="0.00000 0.00000 0.00000"/>
			<mass value="0.00000"/>
			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
		</inertial>
	</link>
	<link name="lfs">
		<inertial>
			<origin rpy="0.00000 -0.00000 0.00000" xyz="0.00000 0.00000 0.00000"/>
			<mass value="0.60000"/>
			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
		</inertial>
		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
	</link>
	<link name="link1_4">
		<inertial>
			<origin rpy="0.00000 -0.00000 0.00000" xyz="0.00000 0.00000 0.00000"/>
			<mass value="0.00000"/>
			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
		</inertial>
	</link>
	<link name="lfk">
		<inertial>
			<origin rpy="0.00000 -0.00000 0.00000" xyz="0.00000 0.00000 0.00000"/>
			<mass value="1.70000"/>
			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
		</inertial>
		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
	</link>
	<link name="link1_6">
		<inertial>
			<origin rpy="0.00000 -0.00000 0.00000" xyz="0.00000 0.00000 0.00000"/>
			<mass value="0.00000"/>
			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
		</inertial>
	</link>
	<link name="rfs">
		<inertial>
			<origin rpy="0.00000 -0.00000 0.00000" xyz="0.00000 0.00000 0.00000"/>
			<mass value="0.60000"/>
			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
		</inertial>
		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
	</link>
	<link name="link1_8">
		<inertial>
			<origin rpy="0.00000 -0.00000 0.00000" xyz="0.00000 0.00000 0.00000"/>
			<mass value="0.00000"/>
			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
		</inertial>
	</link>
	<link name="rfk">
		<inertial>
			<origin rpy="0.00000 -0.00000 0.00000" xyz="0.00000 0.00000 0.00000"/>
			<mass value="1.70000"/>
			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
		</inertial>
		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
	</link>
	<link name="link1_10">
		<inertial>
			<origin rpy="0.00000 -0.00000 0.00000" xyz="0.00000 0.00000 0.00000"/>
			<mass value="0.00000"/>
			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
		</inertial>
	</link>
	<link name="lbs">
		<inertial>
			<origin rpy="0.00000 -0.00000 0.00000" xyz="0.00000 0.00000 0.00000"/>
			<mass value="0.60000"/>
			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
		</inertial>
		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
	</link>
	<link name="link1_12">
		<inertial>
			<origin rpy="0.00000 -0.00000 0.00000" xyz="0.00000 0.00000 0.00000"/>
			<mass value="0.00000"/>
			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
		</inertial>
	</link>
	<link name="lbk">
		<inertial>
			<origin rpy="0.00000 -0.00000 0.00000" xyz="0.00000 0.00000 0.00000"/>
			<mass value="1.70000"/>
			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
		</inertial>
		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
	</link>
	<link name="link1_14">
		<inertial>
			<origin rpy="0.00000 -0.00000 0.00000" xyz="0.00000 0.00000 0.00000"/>
			<mass value="0.00000"/>
			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
		</inertial>
	</link>
	<link name="rbs">
		<inertial>
			<origin rpy="0.00000 -0.00000 0.00000" xyz="0.00000 0.00000 0.00000"/>
			<mass value="0.60000"/>
			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
		</inertial>
		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
	</link>
	<link name="link1_16">
		<inertial>
			<origin rpy="0.00000 -0.00000 0.00000" xyz="0.00000 0.00000 0.00000"/>
			<mass value="0.00000"/>
			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
		</inertial>
	</link>
	<link name="rbk">
		<inertial>
			<origin rpy="0.00000 -0.00000 0.00000" xyz="0.00000 0.00000 0.00000"/>
			<mass value="1.70000"/>
			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
		</inertial>
		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
	</link>
	<joint name="lfsj" type="continuous">
		<parent link="torso"/>
		<child link="link1_2"/>
		<dynamics damping="1.0" friction="0.0001"/>
		<origin rpy="0.00000 -0.00000 0.00000" xyz="-0.04850 0.05050 0.00000"/>
		<axis xyz="1.00000 0.00000 0.00000"/>
	</joint>
	<joint name="jointfix_1_2" type="fixed">
		<parent link="link1_2"/>
		<child link="lfs"/>
		<dynamics damping="1.0" friction="0.0001"/>
		<origin rpy="0.00000 -0.00000 0.00000" xyz="0.00000 0.02300 0.00000"/>
		<axis xyz="0.00000 0.00000 0.00000"/>
	</joint>
	<joint name="lfkj" type="continuous">
		<parent link="lfs"/>
		<child link="link1_4"/>
		<dynamics damping="1.0" friction="0.0001"/>
		<origin rpy="0.00000 -0.00000 0.00000" xyz="0.00750 0.02300 0.00000"/>
		<axis xyz="1.00000 0.00000 0.00000"/>
	</joint>
	<joint name="jointfix_0_4" type="fixed">
		<parent link="link1_4"/>
		<child link="lfk"/>
		<dynamics damping="1.0" friction="0.0001"/>
		<origin rpy="0.00000 -0.00000 0.00000" xyz="0.00000 0.02425 0.00000"/>
		<axis xyz="0.00000 0.00000 0.00000"/>
	</joint>
	<joint name="rfsj" type="continuous">
		<parent link="torso"/>
		<child link="link1_6"/>
		<dynamics damping="1.0" friction="0.0001"/>
		<origin rpy="0.00000 -0.00000 0.00000" xyz="0.04850 0.05050 0.00000"/>
		<axis xyz="1.00000 0.00000 0.00000"/>
	</joint>
	<joint name="jointfix_3_6" type="fixed">
		<parent link="link1_6"/>
		<child link="rfs"/>
		<dynamics damping="1.0" friction="0.0001"/>
		<origin rpy="0.00000 -0.00000 0.00000" xyz="0.00000 0.02300 0.00000"/>
		<axis xyz="0.00000 0.00000 0.00000"/>
	</joint>
	<joint name="rfkj" type="continuous">
		<parent link="rfs"/>
		<child link="link1_8"/>
		<dynamics damping="1.0" friction="0.0001"/>
		<origin rpy="0.00000 -0.00000 0.00000" xyz="-0.00750 0.02300 0.00000"/>
		<axis xyz="1.00000 0.00000 0.00000"/>
	</joint>
	<joint name="jointfix_2_8" type="fixed">
		<parent link="link1_8"/>
		<child link="rfk"/>
		<dynamics damping="1.0" friction="0.0001"/>
		<origin rpy="0.00000 -0.00000 0.00000" xyz="0.00000 0.02425 0.00000"/>
		<axis xyz="0.00000 0.00000 0.00000"/>
	</joint>
	<joint name="lbsj" type="continuous">
		<parent link="torso"/>
		<child link="link1_10"/>
		<dynamics damping="1.0" friction="0.0001"/>
		<origin rpy="0.00000 -0.00000 0.00000" xyz="-0.04850 -0.05050 0.00000"/>
		<axis xyz="1.00000 0.00000 0.00000"/>
	</joint>
	<joint name="jointfix_5_10" type="fixed">
		<parent link="link1_10"/>
		<child link="lbs"/>
		<dynamics damping="1.0" friction="0.0001"/>
		<origin rpy="0.00000 -0.00000 0.00000" xyz="0.00000 -0.02300 0.00000"/>
		<axis xyz="0.00000 0.00000 0.00000"/>
	</joint>
	<joint name="lbkj" type="continuous">
		<parent link="lbs"/>
		<child link="link1_12"/>
		<dynamics damping="1.0" friction="0.0001"/>
		<origin rpy="0.00000 -0.00000 0.00000" xyz="0.00750 -0.02300 0.00000"/>
		<axis xyz="1.00000 0.00000 0.00000"/>
	</joint>
	<joint name="jointfix_4_12" type="fixed">
		<parent link="link1_12"/>
		<child link="lbk"/>
		<dynamics damping="1.0" friction="0.0001"/>
		<origin rpy="0.00000 -0.00000 0.00000" xyz="0.00000 -0.02425 0.00000"/>
		<axis xyz="0.00000 0.00000 0.00000"/>
	</joint>
	<joint name="rbsj" type="continuous">
		<parent link="torso"/>
		<child link="link1_14"/>
		<dynamics damping="1.0" friction="0.0001"/>
		<origin rpy="0.00000 -0.00000 0.00000" xyz="0.04850 -0.05050 0.00000"/>
		<axis xyz="1.00000 0.00000 0.00000"/>
	</joint>
	<joint name="jointfix_7_14" type="fixed">
		<parent link="link1_14"/>
		<child link="rbs"/>
		<dynamics damping="1.0" friction="0.0001"/>
		<origin rpy="0.00000 -0.00000 0.00000" xyz="0.00000 -0.02300 0.00000"/>
		<axis xyz="0.00000 0.00000 0.00000"/>
	</joint>
	<joint name="rbkj" type="continuous">
		<parent link="rbs"/>
		<child link="link1_16"/>
		<dynamics damping="1.0" friction="0.0001"/>
		<origin rpy="0.00000 -0.00000 0.00000" xyz="-0.00750 -0.02300 0.00000"/>
		<axis xyz="1.00000 0.00000 0.00000"/>
	</joint>
	<joint name="jointfix_6_16" type="fixed">
		<parent link="link1_16"/>
		<child link="rbk"/>
		<dynamics damping="1.0" friction="0.0001"/>
		<origin rpy="0.00000 -0.00000 0.00000" xyz="0.00000 -0.02425 0.00000"/>
		<axis xyz="0.00000 0.00000 0.00000"/>
	</joint>
</robot>

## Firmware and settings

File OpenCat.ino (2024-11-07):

/*
   The driver for OpenCat, runs on ATmega328P-based NyBoard (as Arduino Uno).
   Compatible with Petoi Nybble, Bittle, and many other 8 or 12 DoF quadruped robots.
   Drives up to 16 PWM servos.

   Rongzhong Li
   Mar 15rd, 2022
   Copyright (c) 2022 Petoi LLC.

   This sketch may also include others' codes under MIT or other open-source licenses.
   Check those licenses in the corresponding module test folders.
   Feel free to contact us if you find any missing references.

  The MIT License

  Permission is hereby granted, free of charge, to any person obtaining a copy
  of this software and associated documentation files (the "Software"), to deal
  in the Software without restriction, including without limitation the rights
  to use, copy, modify, merge, publish, distribute, sublicense, and/or sell
  copies of the Software, and to permit persons to whom the Software is
  furnished to do so, subject to the following conditions:
  The above copyright notice and this permission notice shall be included in all
  copies or substantial portions of the Software.
  THE SOFTWARE IS PROVIDED "AS IS", WITHOUT WARRANTY OF ANY KIND, EXPRESS OR
  IMPLIED, INCLUDING BUT NOT LIMITED TO THE WARRANTIES OF MERCHANTABILITY,
  FITNESS FOR A PARTICULAR PURPOSE AND NONINFRINGEMENT. IN NO EVENT SHALL THE
  AUTHORS OR COPYRIGHT HOLDERS BE LIABLE FOR ANY CLAIM, DAMAGES OR OTHER
  LIABILITY, WHETHER IN AN ACTION OF CONTRACT, TORT OR OTHERWISE, ARISING FROM,
  OUT OF OR IN CONNECTION WITH THE SOFTWARE OR THE USE OR OTHER DEALINGS IN THE
  SOFTWARE.
*/

/*
  To configure the board:
  1. Select your robot and board version.
  2. Comment out #define MAIN_SKETCH and upload. Upload and follow the serial prompts to proceed.
  3. Uncomment #define MAIN_SKETCH to make it active. Then upload the program for main functions.
*/

#define MAIN_SKETCH  //the Petoi App only works when this mode is on
// #define AUTO_INIT //automatically select 'Y' for the reset joint and IMU prompts
// #define DEVELOPER //to print out some verbose debugging data
// it may increase the code size and crash the bootloader.
// make sure you know ISP and how to reset the bootloader!!!

#define BITTLE  //Petoi 9 DOF robot dog: 1x on head + 8x on leg
// #define NYBBLE  //Petoi 11 DOF robot cat: 2x on head + 1x on tail + 8x on leg

// #define NyBoard_V0_1
// #define NyBoard_V0_2
// #define NyBoard_V1_0
// #define NyBoard_V1_1
#define NyBoard_V1_2

// you can also activate the following modes (they will disable the gyro to save programming space)
// allowed combinations: RANDOM_MIND + ULTRASONIC, RANDOM_MIND, ULTRASONIC, VOICE, CAMERA
// #define RANDOM_MIND  //advanced random behaviors. use token 'z' to activate/deactivate
// #define TASK_QUEUE  //allow executing a sequence of tasks, if you enabled the other modules, the task queue will be automatically enabled. \
                    // because it takes up memory, it will be disabled if the GYRO is enabled. See "#undef TASK_QUEUE" under ifdef GYRO
// #define ULTRASONIC      //for Nybble's ultrasonic sensor
// #define VOICE  //Petoi Grove voice module
// #define VOICE_LD3320    //for LD3320 module
// #define PIR             //for PIR (Passive Infrared) sensor
//#define DOUBLE_TOUCH  //for double touch sensor
//#define DOUBLE_LIGHT  //for double light sensor
// #define DOUBLE_INFRARED_DISTANCE  //for double infrared distance sensor
// #define GESTURE  //for Gesture module
// #define CAMERA  //for human body tracking or ball tracking using an intelligent camera
// You need to install https://github.com/mu-opensource/MuVisionSensor3 as a zip library in Arduino IDE.
// Set the four dial switches on the camera as **v ^ v v** (the second switch dialed up to I2C) and connect the camera module to the I2C grove on NyBoard.
// The battery should be turned on to drive the servos.
//
// You can use these 3D printed structures to attach the camera module.
// https://github.com/PetoiCamp/NonCodeFiles/blob/master/stl/MuIntelligentCamera_mount.stl
// https://github.com/PetoiCamp/NonCodeFiles/blob/master/stl/bone.stl
// After uploading the code, you may need to press the reset buttons on the module and then the NyBoard.
// The tracking demo works the best with a yellow tennis ball or some other round objects. Demo: https://www.youtube.com/watch?v=CxGI-MzCGWM
// #define GROVE_SERIAL_PASS_THROUGH  //allow analog/digital read/write GPIO pins through serial protocol
// #define OTHER_MODULES  //uncomment this line to disable the gyroscope code to save programming resources for other modules.
// #define ROBOT_ARM

#define IR_PIN 4  // Signal Pin of IR receiver to Arduino Digital Pin 4
#include "src/OpenCat.h"

void setup() {
  Serial.begin(BAUD_RATE);
  Serial.setTimeout(SERIAL_TIMEOUT);
  // while (Serial.available() && Serial.read());  // empty buffer

  // join I2C bus (I2Cdev library doesn't do this automatically)
  //#if I2CDEV_IMPLEMENTATION == I2CDEV_ARDUINO_WIRE
  Wire.begin();
  //  TWBR = 24; // 400kHz I2C clock (200kHz if CPU is 8MHz)
  Wire.setClock(500000L);
  //#elif I2CDEV_IMPLEMENTATION == I2CDEV_BUILTIN_FASTWIRE
  //  Fastwire::setup(400, true);
  //#endif
  initRobot();
}

void loop() {
#ifdef MAIN_SKETCH
#ifdef GYRO_PIN
  readEnvironment();     //reads the IMU (Inertia Measurement Unit, i.e. acceleration and angles).
                         //May read more sensors in the future
  dealWithExceptions();  //fall over, lifted, etc.
#endif

#ifdef TASK_QUEUE
  if (!tQueue->empty()) {
    tQueue->popTask();
  } else
#endif
  {
    readSignal();  //commands sent by user interfaces and sensors
#ifdef OTHER_MODULES
    otherModule();  //you can create your own code here
                    //or put it in the readSignal() function of src/io.h
#endif
  }
  reaction();  //handle different commands
#ifdef VOLTAGE_DETECTION_PIN
  lowBattery();  //  block the loop if battery is low
  //  can be disabled to save programming space and reduce the low voltage interruptions
#endif
#else
  calibratePCA9685();
#endif
}

#ifdef OTHER_MODULES  //remember to activate the #define OTHER_MODULES at the begining of this code to activate the following section
int prevReading = 0;
void otherModule() {  //this is an example that use the analog input pin A2 as a touch pad
                      //The A2 pin is in the second Grove socket of the NyBoard
  int currentReading = analogRead(A2);
  if (abs(currentReading - prevReading) > 50) {  //filter noise
    PT("Reading on pin A2:\t");
    PTL(currentReading);
    if (currentReading < 100) {  //touch and hold on the A2 pin until the condition is met
      beep(10, 20, 50, 3);       //make sound within this function body
      tQueue->createTask();      //more tokens are defined in OpenCat.h
    } else {
      strcpy(newCmd, "sit");          //load a skill to be processed by the later reaction function
      if (strcmp(lastCmd, newCmd)) {  //won't repeatively load the same skill
        newCmdIdx = 5;
        token = T_SKILL;  //T_SKILL loads a skill
      }
    }
  }
  prevReading = currentReading;
}
#endif

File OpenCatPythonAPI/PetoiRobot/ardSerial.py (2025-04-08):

#!/usr/bin/python3
# -*- coding: UTF-8 -*-

import struct
import sys
import time
import logging
from .SerialCommunication import *  # module SerialCommunication.py
import platform
import copy
import threading
import os
from . import config
import glob
import re

FORMAT = '%(asctime)-15s %(name)s - %(levelname)s - %(message)s'
'''
Level: The level determines the minimum priority level of messages to log. 
Messages will be logged in order of increasing severity: 
DEBUG is the least threatening, 
INFO is also not very threatening, 
WARNING needs attention, 
ERROR needs immediate attention, 
and CRITICAL means “drop everything and find out what’s wrong.” 
The default starting point is INFO, 
which means that the logging module will automatically filter out any DEBUG messages.
'''
# logging.basicConfig(level=logging.DEBUG, format=FORMAT)
logging.basicConfig(level=logging.INFO, format=FORMAT)
logger = logging.getLogger(__name__)


def printH(head, value):
    print(head, end=' ')
    print(value)


if not config.useMindPlus:
    import tkinter as tk
    import tkinter.messagebox
    sys.path.append("../pyUI")
    from translate import *
    language = languageList['English']

    def txt(key):
        global language
        logger.debug(f"config.strLan is: {config.strLan}.")
        language = languageList[config.strLan]
        return language.get(key, textEN[key])

    # printH("txt('lan'):", txt('lan'))


logger.info("ardSerial date: Feb. 27, 2025")

def encode(in_str, encoding='utf-8'):
    if isinstance(in_str, bytes):
        return in_str
    else:
        return in_str.encode(encoding)

delayBetweenSlice = 0.001

def serialWriteNumToByte(port, token, var=None):  # Only to be used for c m u b I K L o within Python
    # print("Num Token "); print(token);print(" var ");print(var);print("\n\n");
    logger.debug(f'serialWriteNumToByte, token={token}, var={var}')
    in_str = ""
    if var is None:
        var = []
    if token == 'K':
        period = var[0]
        #        print(encode(in_str))
        if period > 0:
            skillHeader = 4
        else:
            skillHeader = 7
            
        if period > 1:
            frameSize = 8  # gait
        elif period == 1:
            frameSize = 16  # posture
        else:
            frameSize = 20  # behavior
    # divide large angles by 2
        angleRatio = 1
        for row in range(abs(period)):
            for angle in var[skillHeader + row * frameSize:skillHeader + row * frameSize + min(16,frameSize)]:
                if angle > 125 or angle < -125:
                    angleRatio = 2
                    break
            if angleRatio ==2:
                break
        
        if angleRatio == 2:
            var[3] = 2
            for row in range(abs(period)):
                for i in range(skillHeader + row * frameSize,skillHeader + row * frameSize + min(16,frameSize)):
                    var[i] //=2
            printH('rescaled:\n',var)
            
        var = list(map(int, var))
        in_str = token.encode() + struct.pack('b' * len(var), *var) + '~'.encode()

    else:
        if token.isupper():# == 'L' or token == 'I' or token == 'B' or token == 'C':
#            if token == 'C':
#                packType = 'B'
#            else:
#                packType = 'b'
#            port.Send_data(token.encode())
            if len(var)>0:
                message = list(map(int, var))
                if token == 'B':
                    for l in range(len(message)//2):
                        message[l*2+1]*= 8  #change 1 to 8 to save time for tests
                        # print(message[l*2],end=",")
                        # print(message[l*2+1],end=",")
                        logger.debug(f"{message[l*2]},{message[l*2+1]}")
            if token == 'W' or token == 'C':
                in_str = struct.pack('B' * len(message), *message)    # B - unsigned char, e.g. 'B'*3 means 'BBB'
            else:
                in_str = struct.pack('b' * len(message), *message)    # b - signed char, e.g. 'b'*3 means 'bbb'
            in_str = token.encode() + in_str + '~'.encode()

        else:#if token == 'c' or token == 'm' or token == 'i' or token == 'b' or token == 'u' or token == 't':
            message = ""
            for element in var:
                message +=  (str(round(element))+" ")
            in_str = token.encode()+encode(message) +'\n'.encode()

    slice = 0
    while len(in_str) > slice:
        if len(in_str) - slice >= 20:
            port.Send_data(in_str[slice:slice+20])
        else:
            port.Send_data(in_str[slice:])
        slice+=20
        time.sleep(delayBetweenSlice)
    logger.debug(f"!!!! {in_str}")
            #print(encode(in_str))
#            port.Send_data(encode(message))


def serialWriteByte(port, var=None):
    logger.debug(f'serial_write_byte, var={var}')
    if var is None:
        var = []
    token = var[0][0]
    # printH("token:",token)
    # print var
    if (token == 'c' or token == 'm' or token == 'i' or token == 'b' or token == 'u' or token == 't') and len(var) >= 2:
        in_str = ""
        for element in var:
            in_str = in_str + element + " "
        in_str += '\n'
    elif token == 'L' or token == 'I':
        if len(var[0]) > 1:
            var.insert(1, var[0][1:])
        var[1:] = list(map(int, var[1:]))
        in_str = token.encode() + struct.pack('b' * (len(var) - 1), *var[1:]) + '~'.encode()
    elif token == 'w' or token == 'k' or token == 'X' or token == 'g':
        in_str = var[0] + '\n'
    else:
        in_str = token + '\n'
    logger.debug(f"!!!!!!! {in_str}")
    # printH("in_str:", in_str)
    port.Send_data(encode(in_str))
    time.sleep(0.01)
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

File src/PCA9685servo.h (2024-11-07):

/***************************************************
  This is an example for our Adafruit 16-channel PWM & Servo driver
  Servo test - this will drive 8 servos, one after the other on the
  first 8 pins of the PCA9685

  Pick one up today in the adafruit shop!
  ------> http://www.adafruit.com/products/815

  These drivers use I2C to communicate, 2 pins are required to
  interface.

  Adafruit invests time and resources providing this open source code,
  please support Adafruit and open-source hardware by purchasing
  products from Adafruit!

  Written by Limor Fried/Ladyada for Adafruit Industries.
  BSD license, all text above must be included in any redistribution
 ****************************************************/

/*
  Revised for conveniently writing angles and setting different servos with different parameters.

  Rongzhong Li
  Feb.2, 2022
*/
#include "Adafruit-PWM-Servo-Driver-Library/Adafruit_PWMServoDriver.h"

#define P_STEP 32
#define P_BASE 3000 + P_STEP * 4  //3128  range: 3000~3320 
#define P_HARD (P_BASE + P_STEP * 1)
#define P_SOFT (P_BASE - P_STEP * 2)

#define SERVO_FREQ 240
#ifndef PWM_READ_PIN
#define PWM_READ_PIN A3
#endif

#define F_MIN 23000
#define F_MAX 27500
#define MATCHING_TIMES 2
#define COUNT_TIMES 7

bool calibrated = false;
int lastValue = 0;

// Depending on your servo make, the pulse width min and max may vary, you
// want these to be as small/large as possible without hitting the hard stop
// for max range. You'll have to tweak them as necessary to match the servos you
// have!

class ServoModel {
public:
  ServoModel(int range, int freq, int min, int max)
    : angleRange(range), frequency(freq), minPulse(min), maxPulse(max) {}
  int angleRange;
  int frequency;
  int minPulse;
  int maxPulse;
};

class Petoi_PWMServoDriver : public Adafruit_PWMServoDriver {
private:
#ifndef MAIN_SKETCH
  const static int SERVOMIN = 150;     // This is the 'minimum' pulse length count (out of 4096)
  const static int SERVOMAX = 600;     // This is the 'maximum' pulse length count (out of 4096)
  const static int USMIN = 600;        // This is the rounded 'minimum' microsecond length based on the minimum pulse of 150
  const static int USMAX = 2400;       // This is the rounded 'maximum' microsecond length based on the maximum pulse of 600
  const static int DEFAULT_FREQ = 50;  // Analog servos run at ~50 Hz updates
  const static int ANGLE_RANGE = 180;
#endif
  const static long OSCILLATOR_FREQ = 25000000;
public:
  int servoPWMFreq;
  long oscillatorFreq;
  float k_us2pulse;
  float b_offset;
  float *k_angle2pulse;

  using Adafruit_PWMServoDriver::Adafruit_PWMServoDriver;

  void setup(int8_t numServo = DOF, long oscillatorFreq = OSCILLATOR_FREQ) {

    setPWMFreq(SERVO_FREQ);
    this->oscillatorFreq = oscillatorFreq;
    setOscillatorFrequency(oscillatorFreq);

#ifndef MAIN_SKETCH
    servoPWMFreq = SERVO_FREQ;
    b_offset = servoPWMFreq / DEFAULT_FREQ * SERVOMIN;
    EEPROM.update(B_OFFSET, byte(b_offset / 10));
    delay(5);
    k_us2pulse = microsecondsToPulse(1);
    //pulse = angle * k_angle2pulse + b_offset
    k_angle2pulse = new float[numServo];
    //servo parameters
    ServoModel servoG41(180, SERVO_FREQ, 500, 2500);
    ServoModel servoP1S(270, SERVO_FREQ, 500, 2500);  //1s/4 = 250ms 250ms/2500us=100Hz
    for (int s = 0; s < numServo; s++) {
      ServoModel *model;
      switch (servoModelList[s]) {
        case G41:
          model = &servoG41;
          break;
        case P1S:
          model = &servoP1S;
          break;
      }

      zeroPosition[s] = model->angleRange / 2 + float(eeprom(MID_SHIFT, s)) * eeprom(ROTATION_DIRECTION, s);
      calibratedZeroPosition[s] = zeroPosition[s] + float(eeprom(CALIB, s)) * eeprom(ROTATION_DIRECTION, s);
      EEPROMWriteInt(ZERO_POSITIONS + s * 2, zeroPosition[s]);
      EEPROMWriteInt(CALIBRATED_ZERO_POSITIONS + s * 2, calibratedZeroPosition[s]);
      EEPROMWriteInt(ANGLE2PULSE_FACTOR + s * 2, int(calcAngleToPulseFactor(s, model->angleRange, model->minPulse, model->maxPulse) * 1000));
    }
#endif
  }
#ifndef MAIN_SKETCH
  float microsecondsToPulse(uint16_t microseconds) {
    float pulse = microseconds;
    float pulselength;
    pulselength = 1000000;  // 1,000,000 us per second
    // Read prescale
    uint16_t prescale = readPrescale();
    // Calculate the pulse for PWM based on Equation 1 from the datasheet section 7.3.5
    prescale += 1;
    pulselength *= prescale;
    pulselength /= oscillatorFreq;
    pulse /= pulselength;
    return pulse;
  }

  float calcAngleToPulseFactor(uint8_t servoNum, int angleRange = ANGLE_RANGE, int usMin = USMIN, int usMax = USMAX) {
    //  angle *  ______________k_angle2pulse______________ + _______________b_offset_______________
    // (angle * (usMax - usMin) / angleRange) * k_us2pulse + servoPWMFreq / DEFAULT_FREQ * SERVOMIN;
    k_angle2pulse[servoNum] = (usMax - usMin) / angleRange * k_us2pulse;
    return k_angle2pulse[servoNum];
    //      Serial.print(servoNum); Serial.print('\t');
    //      Serial.println(k_angle2pulse[PWM_pin[servoNum]]);
  }
#endif
  void writeAngle(uint8_t servoNum, float angle) {
    int clipped = min(max(EEPROMReadInt(ANGLE2PULSE_FACTOR + servoNum * 2) / 1000.0 * angle + (byte)eeprom(B_OFFSET) * 10, 500), 2500);
    setPWM(eeprom(PWM_PIN, servoNum), 0, clipped);
    //      if (servoNum == 1) {
    //        Serial.print(servoNum); Serial.print('\t');
    //        Serial.print(EEPROMReadInt(ANGLE2PULSE_FACTOR + servoNum * 2) / 1000.0 * angle + (byte)eeprom(B_OFFSET) * 10); Serial.print('\t');
    //        Serial.println(clipped);
    //      }
  }
  void shutServos(byte s0 = 0, byte s1 = DOF) {
    //todo:
    //shutServos() all shut
    //shutServos(x) shut x
    //shutServos(a, b) shut a to b
    for (byte s = s0; s < s1; s++) {
      setPWM(s, 0, 4096);
    }
    servoOff = true;
  }
};

// called this way, it uses the default address 0x40
Petoi_PWMServoDriver pwm = Petoi_PWMServoDriver();
// you can also call it with a different address you want
//Petoi_PWMServoDriver pwm = Petoi_PWMServoDriver(0x41);
// you can also call it with a different address and I2C interface
//Petoi_PWMServoDriver pwm = Petoi_PWMServoDriver(0x40, Wire);

void setServoP(unsigned int p) {
  for (byte i = 0; i < 16; i++)
    pwm.writeMicroseconds(i, p);
}
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

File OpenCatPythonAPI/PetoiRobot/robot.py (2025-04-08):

#  -*- coding: UTF-8 -*-

# MindPlus
# Python
from .ardSerial import *
from .SerialCommunication import *
import struct
import time
import re
import platform
import os

intoCameraMode = False

if platform.system() == "Windows":    # for Windows
    seperation = '\\'
    homeDri = os.getenv('HOMEDRIVE') 
    homePath = os.getenv('HomePath') 
    configDir = homeDri + homePath
else:  # for Linux & macOS
    seperation = '/'
    home = os.getenv('HOME') 
    configDir = home 
configDir = configDir + seperation +'.config' + seperation +'Petoi'

modelName = 'Bittle'

# use to print debug information
def printH(head, value):
    print(head, end=' ')
    print(value)

printH("Mind+ date: ", "Feb 25, 2025")


def makeDirectory(path):
    # delete spaces in the path string
    path = path.strip()
    # delete the '\' at the end of path string
    path = path.rstrip("\\").rstrip("/")
    # path = path.rstrip("/")
	
    # check whether the path exists
    isExists = os.path.exists(path)
    
    if not isExists:
        # printH("model name:", path.split(seperation)[-1])
        if path.split(seperation)[-1] == "BittleX+Arm":
            path = seperation.join(path.split(seperation)[:-1]) + seperation + "BittleR"
            # printH("path:", path)
            if not os.path.exists(path):
                # Create the directory if it does not exist
                path = seperation.join(path.split(seperation)[:-1]) + seperation + "BittleX+Arm"
                os.makedirs(path)
                print(path + ' creat successfully')
            else:
                # Change the directory name "BittleR" to "BittleX+Arm"
                os.rename(path,seperation.join(path.split(seperation)[:-1]) + seperation + "BittleX+Arm")
                # print("Rename successfully!")
        else:
            # Create the directory if it does not exist
            os.makedirs(path)
            print(path + ' creat successfully')
        return True
    else:
        # If the directory exists, it will not be created and prompt that the directory already exists.
        print(path + ' already exists')
        return False

makeDirectory(configDir)

def file_name(file_dir):
    # printH("file_dir:",file_dir)
    File_Name=[]
    for files in os.listdir(file_dir):
        # printH("files:",files)
        if os.path.splitext(files)[1] == '.md':
            File_Name.append(files.split('.')[0])
            # printH("File_Name:",files.split('.')[0])
    return File_Name


BittleData = '# Token\n\
K\n\
\n\
# Data\n\
{\n\
  -5,  0,   0, 1,\n\
   1,  2,   3,\n\
   0,-20, -60,   0,   0,   0,   0,   0,  35,  30, 120, 105,  75,  60, -40, -30,     4, 2, 0, 0,\n\
  35, -5, -60,   0,   0,   0,   0,   0, -75,  30, 125,  95,  40,  75, -45, -30,    10, 0, 0, 0,\n\
  40,  0, -35,   0,   0,   0,   0,   0, -60,  30, 125,  95,  60,  75, -45, -30,    10, 0, 0, 0,\n\
   0,  0, -45,   0,  -5,  -5,  20,  20,  45,  45, 105, 105,  45,  45, -45, -45,     8, 0, 0, 0,\n\
   0,  0,   0,   0,   0,   0,   0,   0,  30,  30,  30,  30,  30,  30,  30,  30,     5, 0, 0, 0,\n\
};'

NybbleData = '# Token\n\
K\n\
\n\
# Data\n\
{\n\
  -5,   0,   0,   1,\n\
   2,   3,   3,\n\
   0, -20, -65,   0,   0,   0,   0,   0,  30,  30, -90, -90,  60,  60,  45,  45,   8,   1,   0,   0,\n\
   0, -20, -65,   0,   0,   0,   0,   0,  30,  41, -90, -72,  60,  46,  45,   5,   8,   2,   0,   0,\n\
  35, -15, -65,   0,  -3,  -3,   3,   3, -75,  41, -85, -72,  40,  65,  60,   0,   8,   0,   0,   0,\n\
  40, -10, -55,   0,  -3,  -3,   3,   3, -60,  41, -80, -79,  60,  65,  60,   0,   4,   0,   0,   0,\n\
   0,   0,   0,   0,   0,   0,   0,   0,  30,  41, -30, -30,  30,  30, -30, -30,  12,   0,   0,   0,\n\
};'

BittleRData = '# Token\n\
K\n\
\n\
# Data\n\
{\n\
  -6, 0, 0, 1,\n\
   1, 2, 3,\n\
   0, -20,   0,   0,   0,   0,   0,   0,  35,  30, 120, 105,  75,  60, -40, -30,	 8, 2, 0, 0,\n\
  -5,  -5,   0,   0,   0,   0,   0,   0, -99,  30, 125,  95,  40,  75, -45, -30,	10, 0, 0, 0,\n\
   0,  -5,   0,   0,   0,   0,   0,   0, -90,  30, 125,  95,  62,  75, -45, -30,	10, 0, 0, 0,\n\
 -15,  -5,   0,   0,   0,   0,   0,   0, -90,  30, 125,  95,  62,  75, -45, -30,	 8, 0, 0, 0,\n\
   0,  -5,   0,   0,  -5,  -5,  20,  20,  45,  45, 105, 105,  45,  45, -45, -45,	 8, 0, 0, 0,\n\
   0,   0,   0,   0,   0,   0,   0,   0,  30,  30,  30,  30,  30,  30,  30,  30,	 8, 0, 0, 0,\n\
};'

modelDict = {'Bittle': BittleData, 'Nybble': NybbleData, 'BittleX+Arm': BittleRData,}  # 'BittleR': BittleRData, 

def creatSkillFile():
    for key in modelDict:
        modelDir = configDir + seperation + 'SkillLibrary' + seperation + key
        makeDirectory(modelDir)
        filePath = modelDir + seperation + 'skillFileName.md'
        if not os.path.exists(filePath):
            try:
                with open(filePath, 'w+', encoding="utf-8") as f:
                    f.write(modelDict[key])
                    time.sleep(0.1)
            except Exception as e:
                return False, 'save failed:{}'.format(e)

creatSkillFile()


'''
def getPortList():
    if isinstance(goodPorts, dict):
        p = list(goodPorts.keys())
    elif isinstance(goodPorts, list):
        p = goodPorts
    return p
'''


# deactivate the gyro
def deacGyro():
    boardVer = config.version_
    # printH("boardVer:", boardVer)
    if boardVer[0] == 'N':
        res = send(goodPorts, ['G', 0])
        # printH("gyro status:",res )
        logger.debug(f'gyro status:{res}')
        if res != -1 and res[0][0] == 'G':
            res = send(goodPorts, ['G', 0])
            # printH("gyro status:",res )
            logger.debug(f'gyro status:{res}')
    else:
        res = send(goodPorts, ['gb', 0])
        if res != -1 and res[0][0] == 'g':
            logger.debug(f'gyro is deactived successfully.')


# get the current angle list of all joints
def getAngleList():
    token = 'j'
    task = [token, 0]
    # in_str = token + '\n'
    # com.Send_data(encode(in_str))
    # rawData = checkResponse(token)
    # p = getPortList()
    # rawData = sendTask(goodPorts, p[0], task)
    rawData = send(goodPorts, task)

    logger.debug(f'rawData={rawData}')
    p = re.compile(r'^(.*),',re.MULTILINE)
    for one in p.findall(rawData[1]):
        angle = re.sub('\t','',one)
    strAngleList = angle.split(',')
    logger.debug(f'strAngleList={strAngleList}')
    angleList = list(map(lambda x:int(x),strAngleList)) #angle value have to be integer
    logger.debug(f'angleList={angleList}')
    return angleList
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

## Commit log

2021-01-20 Update OpenCat.ino
    fixed the crazy behavior after failed roll recover.
    [OpenCat.ino]
2021-01-28 allow lower case y for yes
2021-02-13 fixed the bug that Bittle will randomly move one joint after rolling recover. the cause is the MPU overflow. the fix is to send the large angle to an unused joint. in the future it can be fixed by ad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
    [OpenCat.ino]
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2021-02-16 uploaded the demo code for the RGB LED ultrasonic sensor
2021-02-16 added demos for mic, light, touch, reflection, PIR sensor
2021-02-16 added demo for gesture sensor
2021-02-17 fix a bug in the calibration code
    previously all the joints would rotate right after sending calibration signal for one joint.
    the target joint may rotate again and get away from the calibration position.
    [OpenCat.h, OpenCat.ino]
2021-02-19 added the sample code for the seven onboard RGB LEDs
2021-03-01 changed the behavior's frame trigger logic
2021-03-01 refactor the token symbols
    Replaced the token characters with T_XXX as suggested by Alex Young @regularfry
    [OpenCat.h, OpenCat.ino]
2021-03-24 disable the gyro in calibration mode
2021-04-15 Missing lookup pre def posture
    [ESP8266WiFiController.ino]
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2021-04-16 Stop button went missing
2021-04-17 Missing resending page on action and on calibrate
    [ESP8266WiFiController.ino]
2021-04-24 won't erase mpu calibration automatically
2021-06-05 remove pitch exception lifted changed voltage check moved variables to OpenCat.h
2021-06-06 changed gait and sensor reaction
    add play dead skill;
    removed run gait;
    avoid colliding with body during walk, crawl and trot;
    remove buggy tilt reaction;
    add sound&light sensor auto detection；
    add reaction to sound;
    [OpenCat.h, OpenCat.ino]
2021-06-07 play dead, gaits, sensory data
    added play dead trick;
    optimized gaits to avoid self colliding;
    added more actions with sound and light data;
    [SoundAndLightBehavior.csv]
2021-06-09 tuned the voltage blocker for older NyBoard V0
    [SoundAndLightBehavior.csv]
2021-06-23 make ultrasonic test for Bittle Sensor Pack ultrasonic sensor
2021-06-28 print model name
    1. print out the activated model: Bittle or Nybble
    2. move the definition of I2C EEPROM from instinct.h to OpenCat.h
2021-06-29 disable the sound and light sensor
    1. disable the sound and light sensor (experimental) in OpenCat.h
    2. reset the mpu offsets if the writeInstinct.ino is in autorun mode for batch processing.
    [OpenCat.ino]
2021-07-21 fix bugs and add logger
    [ardSerial.py]
2021-08-18 activated the sound and light sensor
2021-08-24 fix a bug when updatign lastCmd
    the location of updating lastCmd is moved outside the "if (token == T_SKILL)" block, so that single character tokens can be updated to lastCmd. Otherwise the robot may not respond to it.
    [OpenCat.ino]
2021-08-25 M token; IR key
    Added an 'M' token to move multiple indexed joints to angles (ASCII format entered in the serial monitor) simultaneously;
    Re-arranged the IR key for the new customized IR panel.
2021-08-31 model name; shorter IR code
    * Moved the device's model info (Nybble/Bittle) to the top of booting printouts.
    * Added a shorter encoding for the IR remote to save flash by about 178 Bytes.
    [OpenCat.ino]
2021-09-09 print calibration offsets before moving
    Print the list of calibration offsets before the joints' movements to help the App read the values.
2021-09-10 print EoL after calibration
    print EoL as "end of line" signal for the app
2021-09-11 remote EoL
    It doesn't help...
    [OpenCat.h]
2021-09-16 move EEPROM functions
    * Move the EEPROM related functions from WriteInstinct.ino to OpenCat.h.
    * Added a "stand" behavior for Nybble so that it can stand up with its hind legs and tail.
2021-09-18 include IRremote library; un-pause
    * Copied the required files of IRremote library to OpenCat/src/ to help new Arduino users to config the environment.
    * Cancel "pause" of motion if other commands are received.
2021-09-29 print robot's state
    Print the robot's state (paused and gyro) when "g" and "p" is entered:
2021-11-28 add march gait; fix typos
    the march gait works well only when gyro is off
    [OpenCat.h, OpenCat.ino]
2021-12-11 fix "wrong skills"
    fix bug of "wrong skills" messages after g, p
    [OpenCat.ino]
2021-12-29 fix divide by zero in calibratedPWM
    [OpenCat.h]
2021-12-31 fix isssue New serial code doesn't work with RPi hat #16
    fixed the issue New serial code doesn't work with RPi hat #16
    [ardSerial.py]
2022-01-04 Optimized scripts
    Simplified command format, remove '' in the task list for numbers;
    Correct typos
    [ardSerial.py]
2022-01-10 randomly mirror behaviors
    Create a mirror function to allow the robot pick random directions of behaviors. It makes the robot more unpredictable and helps it get rid of an infinite loop, such as failed fall-recovering against a wall.
    [OpenCat.h, OpenCat.ino]
2022-01-30 fix type conversion warnings
    [OpenCat.h]
2022-02-03 shift I2C EEPROM data address
2022-02-05 Add T_PRINT_GYRO 'V'
    Add T_PRINT_GYRO 'V' to toggle printing of Gyro data.
2022-02-28 shift initial I2C EEPROM address
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2022-03-22 fix the bug in ordering servoConst
    [OpenCat.ino, imu.h, skill.h]
2022-03-23 tune ultrasonic sensor and random behaviors
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2022-03-25 fix rand int8_t to int
    [reaction.h, ultrasonic.h]
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2022-03-30 fix g p tokens
    [OpenCat.ino, reaction.h, skill.h]
2022-03-31 fix p g button on app
    [reaction.h]
2022-04-04 fix some int8_t cast warnings
    [OpenCat.ino, motion.h, randomMind.h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]
2022-04-06 fix frame = 0 bug
    [OpenCat.h, OpenCat.ino, infrared.h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]
2022-04-11 fix bug with GYRO switch
    [OpenCat.h, imu.h, reaction.h]
2022-04-12 Slow and smooth motion for older NyBoards
    Delay added after skill execution as per discussion here: https://www.petoi.camp/forum/software/opencat-2-0-change-in-servo-designations-won-t-walk-backwards.
    [reaction.h]
2022-04-12 fix the gyro token
    [reaction.h]
2022-04-15 optimize Nybble joint range
2022-04-16 reduce the trigger of low voltage
2022-04-24 correct ardSerial export 16->20
    [ardSerial.py]
2022-04-25 fix changeModel and language bugs
    [OpenCat.h, reaction.h]
2022-04-29 add binders for joint sliders
2022-04-29 get return value from threads
2022-04-30 mirror single frame; fix export loop
2022-05-07 appearance; name trigger
    optimize the layout for Win; name trigger axis; fix bug in the port test;
    [ardSerial.py, translate.py]
2022-05-09 lock size; restart when deleting the last frame
2022-05-12 cancel LED code to save space
2022-05-14 tune gait; fix period loading buffer from EEPROM
    [OpenCat.ino, randomMind.h, reaction.h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]
2022-05-19 add slow start for servos
2022-05-21 add calibration tool to ui.py
2022-05-22 avoid large microsecond signal
    [OpenCat.h, PCA9685servo.h]
2022-05-24 add path for Calibrator.py
2022-05-24 fix blinking picture in calibrator
    [Calibrator.py]
2022-05-28 won't recover if checkGyro is false; make a larger upload button
    [FlashUploader.py, OpenCat.ino, ardSerial.py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]
2022-05-30 swap trigger and delay
    [SkillComposer.py, translate.py]
2022-06-01 correct hex board name
2022-06-01 won't verify after uploading
    [FlashUploader.py]
2022-06-02 fix SkillComposer init random button color
    [SkillComposer.py]
2022-06-02 correct initial posture in SkillComposer
    [Calibrator.py, SkillComposer.py]
2022-06-08 save flash for V0_* boards
2022-06-16 check battery less; rescale K for large angle;
2022-06-18 optimize SkillComposer joint pic
2022-06-20 add rgb color for ultrasonic sensor
2022-07-11 improve pd and rc; avoid dead loop between pd and rc
    [OpenCat.ino, reaction.h]
2022-07-14 raise the signal of soft pid setting
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2022-07-18 abandon wrong pwm calibration module
    [OpenCat.ino, PCA9685servo.h]
2022-07-18 auto decide correct pwm calibration value
    [OpenCat.ino, PCA9685servo.h]
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2022-07-23 won't repeat behavior after falling
    [reaction.h]
2022-07-23 fix jump after fall recover
    [motion.h, reaction.h]
2022-07-23 update ESP8266WiFiController
    Changes:
    1. change click button url on actionpage to be the same page
    2. change action page to api calling which only return response
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2022-07-30 won‘t beep for skills
    [reaction.h]
2022-08-05 fix the case for T_PRINT_GYRO; shorten beep
    [PCA9685servo.h, reaction.h]
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2022-08-24 add simulation model
    reduce the chance of entering the servo's configuration mode, which makes it unresponsive.
    [bittle_simple.urdf]
2022-08-31 reduce flash usage by replace String()
    [PCA9685servo.h]
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2022-09-20 fix delay bug in splitTask
    [ardSerial.py]
2022-09-20 fix bug in splitTaskForLargeAngles
    [ardSerial.py, reaction.h]
2022-10-01 auto init will reset joint calibration
    [skill.h]
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2022-11-04 correct logic for calibration stiffness
    [PCA9685servo.h, reaction.h]
2022-11-28 print token earlier for binary full frame instructions
2022-12-01 improve flip recovery of Nybble
    [PCA9685servo.h]
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2022-12-29 avoid freeze in skill composer
    [OpenCat.h, PCA9685servo.h, SkillComposer.py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]
2023-01-04 avoid shakes when booting
    [OpenCat.h, motion.h]
2023-01-13 fix connection in replug and manual modes
    [ardSerial.py, translate.py]
2023-02-01 add task queue
    allow task sequence in the Arduino code for complex tasks
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2023-02-24 better taskQ
    improve taskQ;
    correct the string length and memcopy of tasks;
    allow binary cmd in taskQ;
    rename balance to up;
    reduce string in gesture;
    [OpenCat.h, OpenCat.ino, camera.h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]
2023-02-24 fix bug in task deletion
    [OpenCat.h, OpenCat.ino]
2023-02-24 fix bug in task->info
    [OpenCat.ino]
2023-02-27 instructions in voice.h. shorten delay in EEPROM; new lastCmd
    add instructions in voice.h.
    shorten delay in EEPROM write to allow short WDT
    fix bug in lastCmd=new char() -> []
    [OpenCat.h, OpenCat.ino, reaction.h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]
2023-02-27 fix cmdLen = 0 out of serialRead
    [reaction.h]
2023-02-27 fix bug in gait direction
    [skill.h]
2023-02-28 fix overflow of K and T
    [reaction.h, skill.h]
2023-02-28 fix bug in comparing calib and newCmd
    [OpenCat.h, reaction.h, skill.h]
2023-02-28 fix ~ endings of newCmd
    [camera.h, randomMind.h, reaction.h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]
2023-03-01 fix ardSerial slice bug; improve io read long
    [OpenCat.h, ardSerial.py, skill.h]
2023-03-01 improve serialRead; reduce skills; disable gyro
    improve serialRead;
    reduce skills;
    disable gyro dial in skillComposer
2023-03-02 safer Mu camera init if it's not connected
2023-03-04 fix long b; fix T K lastCmd
    [OpenCat.ino, ardSerial.py, reaction.h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]
2023-03-05 bootup sound switch
    allow turning off the bootup sound;
    optional damped head motion;
    add macro to inverse servo direction;
2023-03-05 always detect falling; fix back direction
    [imu.h, reaction.h, skill.h]
2023-03-06 move double light init code
    In case the macro is active in the first uploading stage
2023-03-08 correct gyroBalance
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2023-03-10 Nybble eye color; serial control voice
    allow turning off the auto eye color of the ultrasonic module;
    send serial cmd to voice module
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2023-03-10 Revert "forbid violent motions in voice random"
    [skill.h]
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2023-03-18 move exception out of behavior reaction;fix bugs
    move exception case out of behaviors;
    infrared should not set 1-byte string as newCmd;
    printCmdByType() doesn't need cmdLen to print;
    Upper-case tokens (B, C, I, M) may have wrong terminators when entered into the serial monitor;
    [infrared.h, reaction.h]
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2023-03-21 serial pass-through; eye color; tokens.
    add serial pass-through;
    fix eye color bug;
    rename tokens
    [OpenCat.h, OpenCat.ino, RgbUltrasonic.cpp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]
2023-03-21 Thai; update trigger translation
    add the Thai language;
    fix trigger translation bug in SkillComposer
    [SkillComposer.py, reaction.h, translate.py]
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2023-03-25 correct camera setting
2023-04-03 Update imu.h
    halt the setup if DMP fails
    [imu.h]
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2023-04-19 add tolerance for distance sensor
    [doubleInfraredDistance.h]
2023-04-26 avoid entering zero posture when connecting app
    [OpenCat.h]
2023-04-28 deleteDuplicatedUsbSerial
    delete duplicated usbserial if usbmodem exists;
    won't parse result = -1 to avoid exceptions.
    [ardSerial.py]
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2023-05-10 fix macOS can not upload and update the serial port list after re-plugging
    [FirmwareUploader.py, ardSerial.py, translate.py]
2023-05-11 add a Checkbutton for whether uploading the para firmware fix bug in Skill Composer for Checkbuttons Gyro and Random
    [FirmwareUploader.py, SkillComposer.py, translate.py]
2023-05-21 update software serial pin definition
    modify the software serial pins to avoid conflicting with the ultrasonic sensors
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2023-05-26 change the Factory Reset button fg to red
2023-05-26 fix Enable Servo button state not change issue.
    [ardSerial.py]
2023-05-26 correct logic for gyro switches
    [OpenCat.ino, reaction.h]
2023-05-29 fix gyro_Balance logic
2023-06-05 fix exception when changing Board version to BiBoard while mode is Mind+
    [FirmwareUploader.py]
2023-06-05 Update ardSerial.py
    optimize the responseTrim logic to avoid the strange character and result[0]
    [ardSerial.py]
2023-06-20 fix the random jigs during mobile calibration
    [OpenCat.h]
2023-06-20 fix firmware uploading bug for Biboard and update the version to 1.1.0
    [FirmwareUploader.py, translate.py]
2023-07-12 Add creator and location info in Skill Composer fix bugs: config eye led color when click cancle button
    [FirmwareUploader.py, SkillComposer.py, UI.py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]
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2023-07-15 improve stability of hi behavior; del gaits
    [infrared.h]
2023-08-09 fix save creator and location bug on the Mac OS
    [FirmwareUploader.py, SkillComposer.py, UI.py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]
2023-08-11 update firmware for BiBoard to fix Skill Composer bug - switch frame in the action frame list.
2023-08-21 fix upload firmware for BiBoard in the Linux OS.
    [FirmwareUploader.py, UI.py]
2023-08-22 fix the logo is shown in the windows's title.
    [Calibrator.py, FirmwareUploader.py, SkillComposer.py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]
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2023-09-15 add Bittle X in the product list and fix some bugs
    [FirmwareUploader.py]
2023-10-26 fix auto store skill file to .config directory bug
    [SkillComposer.py, ardSerial.py, commonVar.py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]
2023-11-17 fix 8266 master bug
    [test8266Master.ino]
2023-12-06 fix irresponsive mobile button after sending XA*
    [OpenCat.h]
2023-12-29 Update OpenCat.h
    Remove multiline comment causing error
    [OpenCat.h]
2024-01-09 release the version 1.1.6
    1. Suport factory reset function for BiBoard
    2. Update the firmware of BiBoard, which can change volume via serial command
    [FirmwareUploader.py, ardSerial.py, commonVar.py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]
2024-01-15 adding support for raspberry pi's and newer OS's
2024-01-23 Add promopt window when opening the Calibrator or Skill Composer
2024-02-02 fix bug
    fix the error message "module 'tkinter' has no attribute 'messagebox'" when run ardSerial.py.
    [ardSerial.py]
2024-02-02 adding serial port 'ttyS0' for raspberry pi's and newer OS's
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2024-02-27 ultrasonic sensor
    Allow reading ultrasonic sensor via serial command
2024-02-28 fix bug of mismatching } in nested switch
    [reaction.h]
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2024-03-01 release for updating firmware to support read ultrasonic distance via Mind+
2024-03-27 Add the python tool for adjusting camera module
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2024-04-02 fix a bug in camera: base front down direction
    [OpenCat.h, camera.h]
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2024-04-16 fix typo of mRUS04
    [reaction.h]
2024-04-18 fix the bug: there are ultrasonic reactions when define GROVE_SERIAL_PASS_THROUGH
    [OpenCat.h]
2024-04-24 fix logic error for serial_passthrough and ultrasonic
    [OpenCat.h]
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2024-05-09 fix error in doubleLight.h
    [OpenCat.h, doubleLight.h]
2024-05-14 To make robot sit at first then calibrate light sensor.
2024-06-28 Add new features
    - record log for upload firmware
    - Add Debugger to reset voice module
    - change to use 4M flash_size to upload BiBoard firmware
    - translate pre-postures name to different languages
    [FirmwareUploader.py, SkillComposer.py, UI.py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]
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2024-07-05 improve the layout of Debugger interface and add the button tips
2024-07-27 After the firmware upload fails, an information prompt box pops up and the folder where the logfile is located is opened.
    [FirmwareUploader.py, translate.py]
2024-07-27 update the pictures of Bittle X wire connection.
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2024-07-29 fix the bug after the model name change to "BittleX"
    [SkillComposer.py]
2024-08-01 fix the bug for NyBoard
    when press Factory Reset button, there is no prompt message box, while the I2c switch is on the wrong side.
    [FirmwareUploader.py]
2024-08-01 Modify Firmware upload process for BiBoard
    * Factory Reset Button:
    After uploading the firmware, it will be forced into configuration mode. For questions, the user needs to manually select the yes or no button.
    * Upgrade button:
    After uploading the firmware, it is not forced to enter the configuration mode, but if it is in the configuration mode, it will automatically reply No to skip the prompt question.
    [FirmwareUploader.py]
2024-08-06 A bug in the SkillComposer
    There is a bug in Skill Composer, when switch language after changing model
    [Calibrator.py, Debugger.py, FirmwareUploader.py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]
2024-08-06 fix modelName; rebuild controller
    [SkillComposer.py, ardSerial.py, commonVar.py]
2024-08-06 fix modelname and changing model or language bug
    [Calibrator.py, SkillComposer.py, ardSerial.py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]
2024-08-06 fix calibrator and menu
    [Calibrator.py, SkillComposer.py, UI.py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]
2024-08-06 fix typo; allow space in displayName
    [SkillComposer.py, UI.py, commonVar.py]
2024-08-08 Display different wring picture according to different Board version of Bittle R
2024-08-16 Add switch working mode function in Firmware Uploader.
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2024-09-09 update pics and support to robot arm for NyBoard
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2024-09-11 add Bittle X0 pics
    [tool.stl]
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2024-11-07 solve the problem of abnormal exit
    [FirmwareUploader.py, ardSerial.py, translate.py]
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2024-12-12 Average distance readings to reduce sensor noise
    Averaging multiple distance readings stabilises Bittle's otherwise constant servo jitter due to small fluctiations in sensor readings.
    [ultrasonic.h]
2024-12-27 BittleR servo wiring update and fix some bugs.
    - 1. Update the firmware of BiBoard for bug fixing and BittleR servo wiring update.
    - 2. Fix the Gyro state switch button function bug.
    - 3. Update the wiring picture of Bittle R with BiBoard V1.
    - 4. Add the Product Nybble Q.
    [Calibrator.py, FirmwareUploader.py, SkillComposer.py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]
2025-01-02 update the BiBoard firmware for fixing the camera module startup bug.
    [FirmwareUploader.py, SkillComposer.py, translate.py]
2025-01-02 update firmware for BiBoard to fix send XAd to voice module for joint calibration after bootup.
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2025-01-06 update firmware for BiBoard QA parameter and NyBoard pee skill para
2025-02-27 Fix Raspberry Pi 5 can't open serial port issue.
    [ardSerial.py]
2025-04-08 Add gyroscope calibration in Tools
    - Modify name to Bittle X+Arm
    - Change name Debugger to Tools
    - Add gyroscope calibration in Tools
2025-06-23 Update the firmware for the products with BiBoard.
    Change the partition scheme to mini-spiff.
    Fix the bug for translation in Tools.
    [Debugger.py, SkillComposer.py, translate.py]
